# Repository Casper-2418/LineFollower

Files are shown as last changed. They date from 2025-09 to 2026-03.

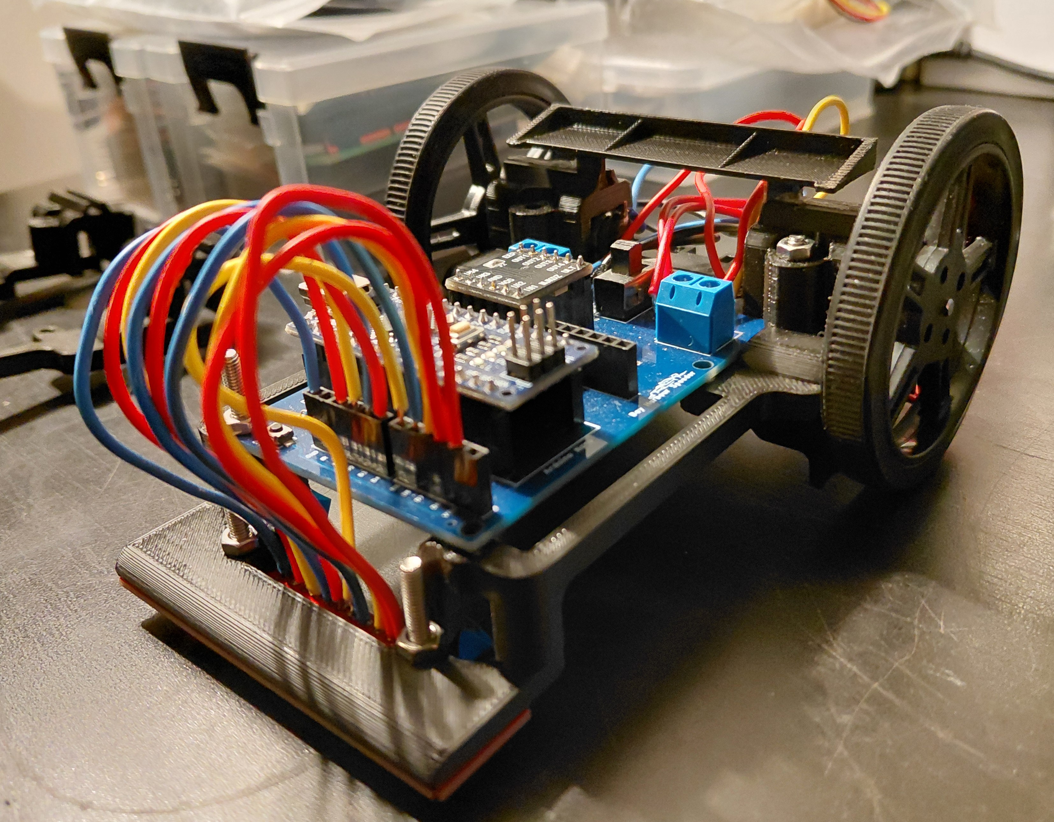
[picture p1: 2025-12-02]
images/20251202_184908.jpg

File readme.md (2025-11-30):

# LineFollower

516304872-0ebdff40-2b66-4d8c-be46-cdccf1087acf

## specifications

microcontroller: Arduino nano (clone)

motors: N20---30:1---500RPM 

h-bridge: DRV8833

sensors: HY-S301

batteries: 2x 18650 lipo

wireless communication: HC-08 

distance sensor - motors: 9.92cm

weight: 214gr

speed: 0.7m/s (voorlopige stabiele snelheid)

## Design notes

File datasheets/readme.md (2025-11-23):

datasheets of the components used in this project

Datasheet van de DRV8833 [drv8833-datasheet.pdf](https://github.com/user-attachments/files/23694670/drv8833-datasheet.pdf)

Datascheet van de Arduino nano [A000005-datasheet.pdf](https://github.com/user-attachments/files/23694715/A000005-datasheet.pdf)

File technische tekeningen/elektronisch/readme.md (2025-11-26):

# PCB ontwerp

a38c5a8e-52b1-4e57-9f7f-d86845e7ee0b

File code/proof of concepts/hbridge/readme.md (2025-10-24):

# H-Bridge proof of concept

Welkom in de readme van het H-brug gedeelte van de linefollower.

De H-brug gebruikt een DRV8833 microchip. Deze heeft op het breakoutbord 4 ingangen, 4 uitgangen, VCC, GND, EEP & ULT.

De ingangen en uitgangen spreeken opzich, zeer belangrijk bij de ingangen is dat de pwm's op de zelfde clock snelheid zitten. PWM 3, 5, 6 & 11 hebben een 8bit clocksnelheid. PWM 9 & 10 hebben een 16bit clocksnelheid. ALs 2 soorten clocksnelheden worden gebruikt zullen de motoren een verschillende snelheid hebben.

De EEP pin wordt aan de VCC (5V) van de arduino gekoppeld, dit moet zeker verbonden worden anders zal de H-brug niet werken. Als de EEP geen voeding krijgt zal de H-brug in sleep modus staan waardoor de OUT's niet zullen schakelen.

De Ult pin wordt met een pull-up weerstand geschakeld, deze dient als fout detectie. Als de H-brug normaal werkt zal deze een hoog signaal hebben waardoor de arduino een laag signaal leest. Als er een interne fout in de H-brug is zal de uitgang laag zijn waardoor de arduino een hoog signaal zal lezen. Dit zullen we a.d.h.v. een HC-05 door sturen naar een gsm.

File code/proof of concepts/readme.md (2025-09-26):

# Proof of Concepts

Een proof of concept is een combinatie van minimale hard- en software om eenvoudig aan te tonen dat iets werkt.  
Proof of concepts kunnen enerzijds als eerste poging dienen om een bepaald onderdeel van het project werkend te krijgen. Anderzijds kunnen ze tijdens het debuggen van het finale project dienen als test om eventuele hardware problemen te elimineren bij onduidelijke problemen.
<br />  
<br />
Een proof of concept bestaat uit
* een elektronisch schema (indien van toepassing)
* minimale code om de voorop gestelde zaken te demonstreren
* minimale uitleg / aandachtspunten
<br />
De elektronische schakelingen van de proof of concepts komen bij voorkeur overeen met deze van de uiteindelijke linefollower, zodat de code zonder aanpassingen op het finale project kan draaien.

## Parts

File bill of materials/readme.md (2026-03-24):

## bill of materials
<br />

|volgnummer|naam|omschrijving|nieuw/recup|kostprijs/stuk|aantal|subtotaal|
|---|----|---|---|---|---|---|
| 1| HC-08 Bluetooth module met adapter - clone| bluetooth module | nieuw | €8.5 |  1 |  €8.5 |
| 2| Arduino Nano R3 - kloon - met headers| Arduino Nano | nieuw |  €8.60 |  1 |  €8.60 |
| 3| Female header stackable 6 pin (5x nodig) |10x Female headers 6 pin | nieuw |  €2.85 | 0.5 | €1.425 |
| 4| DRV8833|dubbele H-brug | nieuw | €3 | 1 |€3 |
| 5| HY-S301 | 8x IR Lijn Tracking Module | nieuw | €3.50 | 1 | €3.50 |
| 6| Aslong JGA12-N20-30 DC-Transmissiemotor 6V - 500RPM| motor 30:1 | nieuw |  €4.50 | 2 |  €9.00 |
| 7| 15 Pins header Female | female headers 15 pins | nieuw |  €0.31 | 2 | €0.62 |
| 8| 18650 | batterij | nieuw | €1.45 | 2 | €2.90 |
| 9| 2x 18650 Batterijhouder met klemkontacten en losse draden | Batterijhouder |  nieuw | €1.59 | 1 |  €1.59 |
| 11| | klemschroefblok 2 pins | recup | €0.55 |  2 |  €1.10 |
| 12| JLCPCB| zelf ontworpen pcb | nieuw | €4.245 |  1 | €4.245 |
| 13|  wielen  | aliexpress wielen | nieuw | €0.98 |  2 | €1.96 |
| | | | | | | |
| Totaal| |  (zonder verzend kosten!!!!!) | | | | €46,44 |

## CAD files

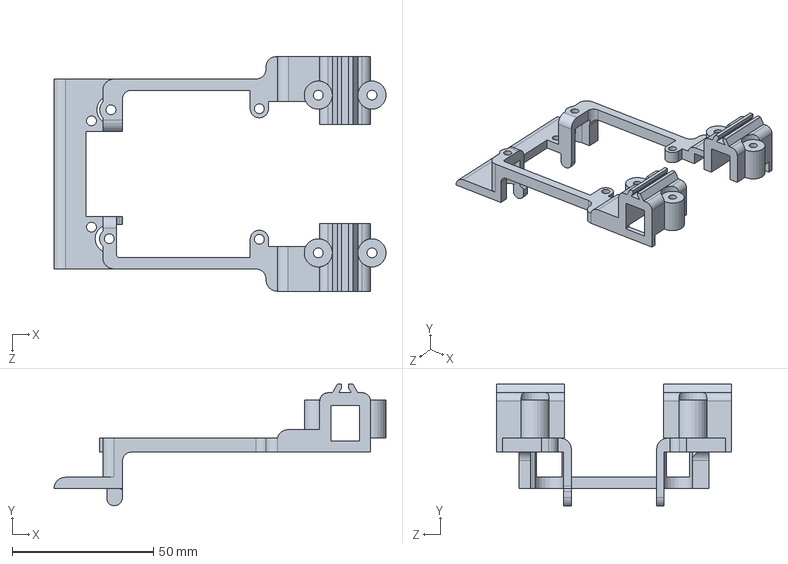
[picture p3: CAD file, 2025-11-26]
technische tekeningen/mechanisch/Frame V9.SLDPRT
117.5 x 43.0 x 83.0 mm

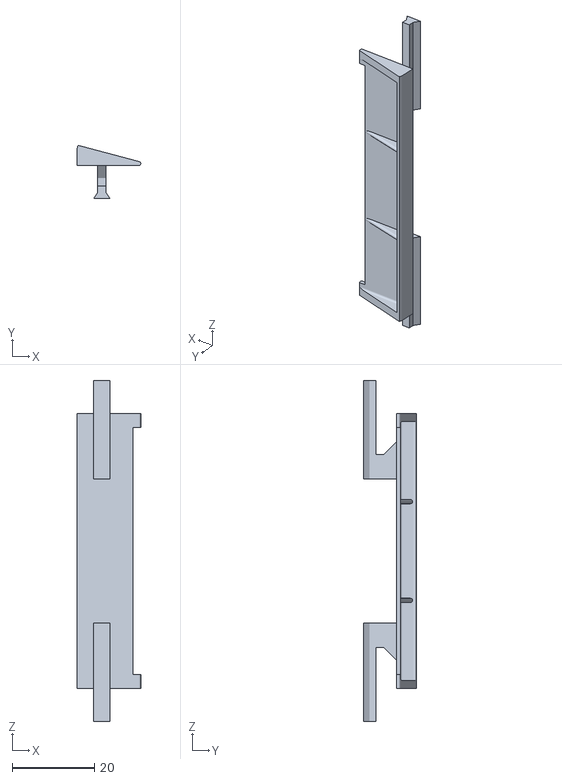
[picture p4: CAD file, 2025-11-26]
technische tekeningen/mechanisch/Spoiler_Casper.STL
15.5 x 12.9 x 83.0

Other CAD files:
technische tekeningen/mechanisch/Frame V9.STL

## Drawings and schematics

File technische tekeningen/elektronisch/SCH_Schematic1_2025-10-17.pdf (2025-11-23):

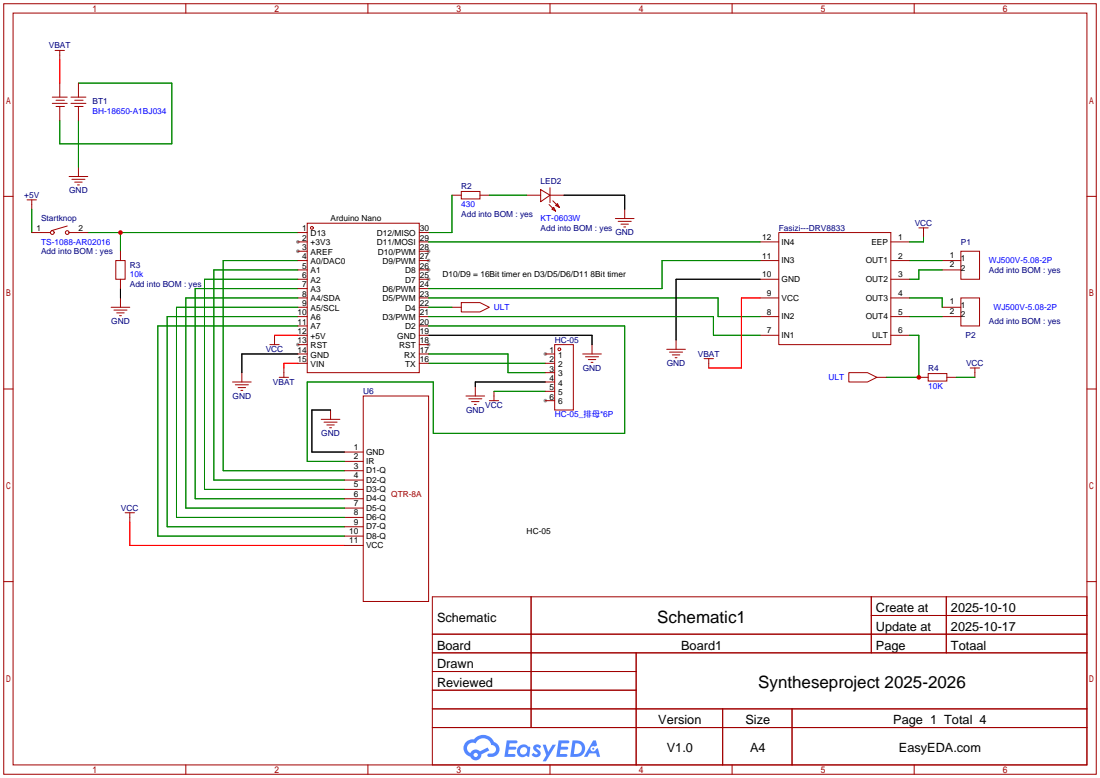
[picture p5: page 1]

Startknop
Add into BOM : yes

Schematic | Schematic1 | Create at | 2025-10-10

Update at | 2025-10-17

Board | Board1 | Page | Totaal
Drawn | | Syntheseproject 2025-2026
Reviewed

Version | Size | Page 1 Total 4
V1.0 | A4 | EasyEDA.com

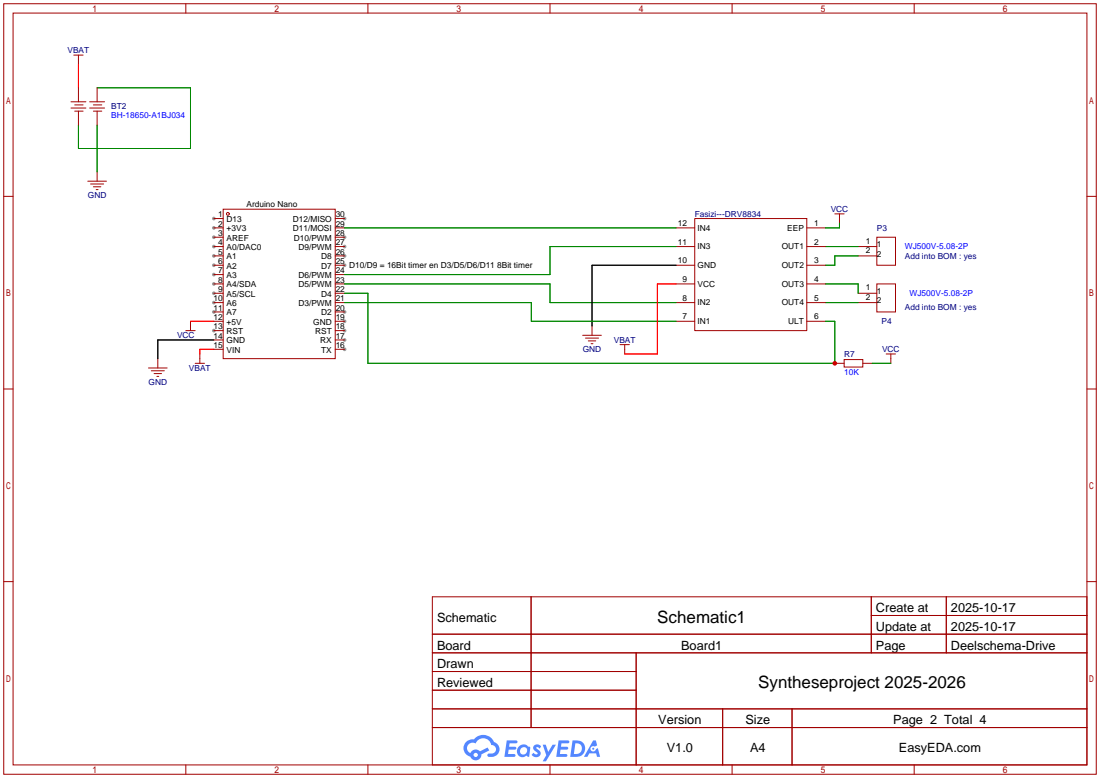
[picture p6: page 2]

Schematic | Schematic1 | Create at | 2025-10-17

Update at | 2025-10-17

Board | Board1 | Page | Deelschema-Drive
Drawn | | Syntheseproject 2025-2026
Reviewed

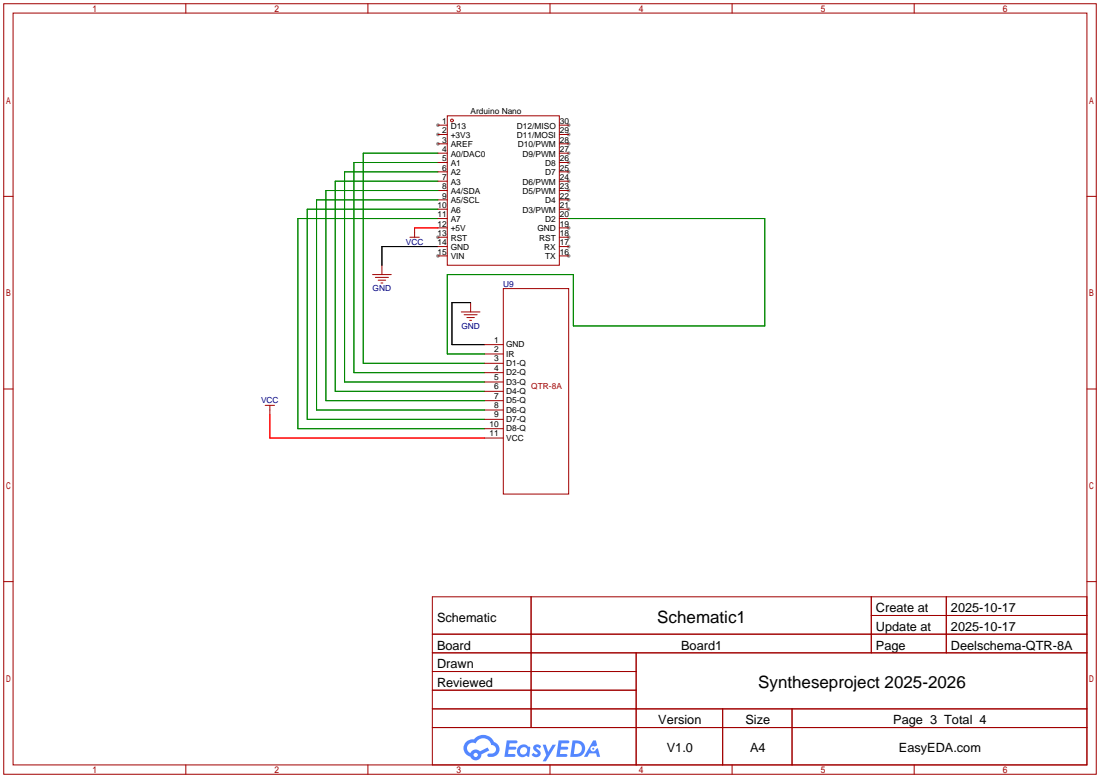
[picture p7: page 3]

Schematic | Schematic1 | Create at | 2025-10-17

Update at | 2025-10-17

Board | Board1 | Page | Deelschema-QTR-8A
Drawn | | Syntheseproject 2025-2026
Reviewed

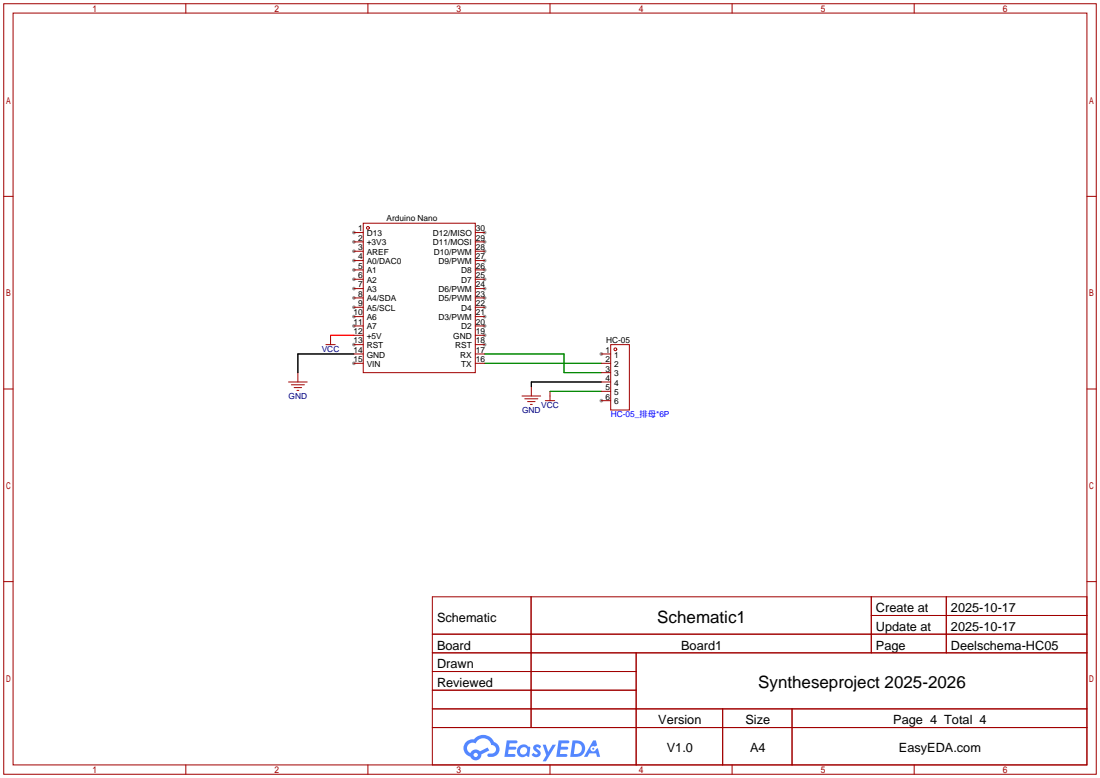
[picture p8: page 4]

Schematic | Schematic1 | Create at | 2025-10-17

Update at | 2025-10-17

Board | Board1 | Page | Deelschema-HC05
Drawn | | Syntheseproject 2025-2026
Reviewed

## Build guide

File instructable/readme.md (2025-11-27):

# Instructable

Een instructable is een stappenplan - zonder verdere uitleg - hoe je vertrekkend van de bill of materials en gebruik makend van de technische tekeningen de robot kan nabouwen. Ook de nodige stappen om de microcontroller te compileren en te uploaden staan beschreven.  

### stap 0
Bestel de componenten uit de BOM, zoveel mogelijk van dezelfde leverancier (tinytronics).

De pcb, onder technische tekeningen -> elektronisch vindt je de elektronische schemas als de pcb file die je kan importeren in easyeada.

De pcb is ontworpen om de weerstanden, drukknop, schakelaar en led er op telaten zetten tijdens productie en is dus mee gerekend in de pcb kosten.
(dit moet je tijdens het bestellen aanduiden want dit wordt niet automatisch gedaan)

### stap 1
test de componenten uit a.d.h.v. de schemas en codes onder de tab code -> proof of concepts. 
deze zullen een goede werking demonstreren van de componenten.

DRV8833 wordt best eerst getest met led's.
Aangeraden om de sensor op een vaste hoogt te monteren om een duidelijk verschil te zien tussen zwart en wit.

### stap 2
Soldeer de female headerds en terminals op de pcb als de draden op de sensor, aangeraden om 0.8mm² stijvedraden te gebruiken (recup van sgg kabel).

### stap 3
Print het frame dat te vinden is onder technische tekeningen -> mechanisch. 
Hier zal je een stl bestand vinden als een solidworks tekening voor als je zelf aanpassingen wilt uitvoeren.
(spoiler stl is ook beschikbaar)

### stap 4
monteer alle componeten op het frame met M3 bouten en moeren. je moet er maar 5 van elk gebruiken (2 voor de sensor, 2 voor de batterijhouder en 1 voor de pcb).

### stap 5
Als de motoren en batterijhouder op het frame zijn bevestigd kan je de draden hiervan solderen.

LET GOED OP!!!!
Batterijhouder: de rode draden van de batterijhouder zullen wij zien als + en zwart als -. We solderen de rode draden op de pcb links van de schakelaar (aan de kant waar VBAT staat) en de zwarte draden rechts van de schakelaar (aan de kant waar GND staat). 
De batterijen zijn via de pcb in serie geschakeld dus we mogen ze extern NIET KRUISEN, ik heb de buitenste batterij aan de buitenste pads gesoldeerd en de batterij aan de binnen kant aan de binnenste pads.

Motoren: de motoren kunnen simpel gesoldeerd worden als ze geklemmed zitten in het frame. hoe dat deze aangesloten worden is de bovenste draden aan de buitenste terminal slots en de onderste aan de binneste slots van hun respectievelijke terminals (links-links & rechts-rechts).

### stap 6 
Upload de basis code dat te vinden is in code->basis. download alle 4 de bestanden en zet deze in dezelfde map. anders zal het programma niet werken.
dit programma bevat een basis werking van het EEPROM geheugen als normalistatie en interpolatie van de sensor en een P regelaar. 

commandes zijn terug tevinden in de gebruikersaanwijzing.

### stap 7
print de parcours. steek de batterijen in de houder (ROOD +, ZWART -) en zet de schakelaar naar binnen toe. 
als alles goed is verlopen zullen nu signalisatie leds van de arduino nano, hc-08 en motordrive branden.

### stap 8
zet de follower op een wit stuk van het parcour en calibreer wit, doe dit ook voor zwart.

Zet intitieel  power= 80, kp= 10 en diff op 0,4.
Nu ben je klaar om te rijden. 
Stuur het commande "run on" and watch the magic happen.

Je zal de instellingen langzaam moeten tweaken want de waarde zullen voor iedereen verschillen.

### stap 9
upload de final code, deze heeft ook een I & D regelaar.
De follower heeft nu de mogelijkheid om de lijn vlotter tevolgen.

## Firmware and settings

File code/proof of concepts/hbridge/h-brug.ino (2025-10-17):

const int IN1 = 5;   // Motor A pin 1
const int IN2 = 6;   // Motor A pin 2
const int IN3 = 9;   // Motor B pin 1
const int IN4 = 10;  // Motor B pin 2

void setup() {
  pinMode(IN1, OUTPUT);
  pinMode(IN2, OUTPUT);
  pinMode(IN3, OUTPUT);
  pinMode(IN4, OUTPUT);
  Serial.begin(9600);
  Serial.println("Twee motoren snelheidsverloop test start");
}

void loop() {
  // snelheid van -255 (achteruit) naar 255 (vooruit)
  for (int snelheid = -255; snelheid <= 255; snelheid++) {
    stelMotorSnelheidIn(IN1, IN2, snelheid);  // Motor A
    stelMotorSnelheidIn(IN3, IN4, snelheid);  // Motor B
    Serial.println(snelheid);
    delay(10); // bepaalt hoe snel de verandering verloopt
  }

  // eventueel even stoppen
  stelMotorSnelheidIn(IN1, IN2, 0);
  stelMotorSnelheidIn(IN3, IN4, 0);
  delay(1000);
}

// ---------- Functie om motorrichting en PWM in te stellen ----------
void stelMotorSnelheidIn(int pin1, int pin2, int snelheid) {
  if (snelheid > 0) {
    analogWrite(pin1, snelheid);
    analogWrite(pin2, 0);
  } else if (snelheid < 0) {
    analogWrite(pin1, 0);
    analogWrite(pin2, -snelheid); // negatief omzetten naar positief
  } else {
    // motor uit
    analogWrite(pin1, 0);
    analogWrite(pin2, 0);
  }
}

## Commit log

2025-10-17 Add files via upload
    Dit is een deel schema voor de h-brug van de line follower, met dit schema en de code zal je 2 motoren aansturen en deze van pwm -255 tot pwm 255 laten draaien. Dit programma en schema test de volled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
2025-11-23 Update and rename easyeda_linefollower_planB.json to PCB ontwerp
2025-11-23 Update and rename PCB ontwerp to -
2025-11-23 Create interrupt test
2025-11-23 Update and rename readme.md to BOM.md
2025-11-26 Update and rename PCB.md to readme.md
